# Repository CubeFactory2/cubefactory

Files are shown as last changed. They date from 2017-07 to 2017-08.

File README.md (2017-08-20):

# CubeFactory 2

The CubeFactory 2 is an autonomous and portable mini factory with own energy and material supply. It embeds three modules: a 3D-printer, a plastic recycler producing filament for the 3D-printer for closed-loop material supply as well as photovoltaic panels and batteries for energy supply. It was developed at the [Department for Assembly Technology and Factory Management of the Technische Universität Berlin](http://www.mf.tu-berlin.de/) in the frame of the [Collaborative Research Center 1026 "Sustainable Manufacturing - Shaping Global Value Creation"](http://www.sustainable-manufacturing.net).

Key figures:
* Weight:
* Dimensions: 801 x 399 x 522 mm
* Autonomy: 8 hours of printing without power supply

In this repository, you will find the complete technical documentation produced in the development of the CubeFactory 2.

## Table of contents

* [About](#about)
* [Components](#components)
* [Contribute](#contribute)
* [License](#license)
* [More information](#more-information)

## About

bild cf2

Especially in Emerging Countries there is a high demand for self-driven value creation. This is caused by an insufficient infrastructure of energy, technology and raw material. Also industrial and humanitarian supply chains are slow, difficult and expensive and equipment for value creation can be expensive and demands skills.
The motivation is that communities affected by a low standard of living or disaster are able to control their situation by manufacturing essential life-saving and life-sustaining supplies by their own.

In general, the CubeFactory 2 has the following purposes:
* Mediation of a sustain value creation
* Production of 3D printed objects by operating with disposable resources to create a sustain product
* Realization of closed loop material cycles
* Low-cost manufacturing of material and product
* Enabling small producers to access markets

## Components

The CubeFactory 2 contains all necessary infrastructure for production. It consists of the following components:
* 3D FDM printer
* Case
* Power supply, consisting of foldable solar panels and accumulator
* Recycler, consisting of PET shredder and extruder

bild cf2 detail

### Cost overview

| Component | Cost in € | Details |
|:----| ----: | :---- |
| 3D-printer | 614 | [printer readme](3d_printer) |
| Case | 250 | [case readme](case) |
| Power supply | 4430<sup>1</sup> | [power supply readme](power_supply) |
| Recycler | 1200<sup>2</sup> | [recycler BOM](recycler/BOM_WeCycler.ods) |
| **Sum** | **6494** ||

**Notes on costs:**  
1: The cost for the power supply is that high because its parts were custom made to fit into the case. Alternative solutions for the power supply such as a plug could significantly reduce the cost to a few hundred Euros.  
2: The prices for the parts of the recycler have not been completely documented yet. Therefore, the above cost for the recycler is estimated.

## Contribute

Feel free to build and futher develop the CubeFactory 2. Any improvements of the work documented here are welcome.
There is a high flexibility in terms of selecting the particular components for the CubeFactory 2. For example, the power could alternatively be sourced from a car battery or generated through wind, water or nuclear fusion. While the 3D-printer is an independent open source project, the Recycler is an own development for the use in the CubeFactory and offers a lot of room for improvement.  

## License

<br />This work is licensed under a <a rel="license" href="http://creativecommons.org/licenses/by-sa/4.0/">Creative Commons Attribution-ShareAlike 4.0 International License</a>.

## More information
* About the previous version of the CubeFactory as well as related projects such as the RecyclerBin: visit the [Cubefactory blog](http://cubefactory.org/).
* About the underlying concept: see the publication ["Realization of a Learning Environment to Promote Sustainable Value Creation in Areas with Insufficient Infrastructure"](http://www.sciencedirect.com/science/article/pii/S2212827115005399) (CC BY-NC-ND 4.0)
* About the results of the Collaborative Research Center "Sustainable Manufacturing - Shaping Global Value Creation": check the book ["Sustainable Manufacturing - Challenges, Solutions and Implementation Perspectives"](https://link.springer.com/book/10.1007/978-3-319-48514-0) (CC BY 4.0)

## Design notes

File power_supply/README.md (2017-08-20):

# Power Supply 

In order to ensure the autonomous operation of the CubeFactory 2, it has a photovoltaic generator and a battery storage system. The following remarks will give you an overview of the most important facts on the subject. 

---

### Contents

 * [Photovoltaic generator](#photovoltaic-generator)
 * [Battery storage system](#battery-storage-system)
 * [Important parameters](#important-parameters)
 * [Equipment](#equipment)
 * [Cost overview](#cost-overview)
 * [Alternative approaches](#alternative-approaches)
 
---

### Photovoltaic generator

The PV generator converts sunlight directly into electrical direct current and allows to operate the printer or charge the battery storage system. The PV generator itself consists of 3 foldable modules, which makes it possible to fit the modules, like all other components, into the case. In this way, the modules can be easily transported and, if necessary, protected against environmental influences.

---

### Battery storage system

In order to store the surplus energy generated by  PV generator, and compensate for irregularities in the power generation, the CubeFactory 2 has a lithium battery.

#### Discharge curve

The discharge curve describes the relationship between remaining capacity and operating voltage. The characteristic feature of lithium batteries is that they supply a constant voltage over the entire discharge period. The following figure shows the charging curve for a lithium battery for different C values.

N|Kurve2

The mentioned C-value indicates the factor of the battery charge quantity that is discharged per hour.

#### Calculation of the required charge quantity

The CubeFactory's battery is designed to operate the 3D printer for about *t=8* hours. In order to determine the required charge quantity *Q* the power consumption *P* and the electricity consumption *i* of the 3D printer must be known. In the case of our printer *P = 100 W* and *I = 10 A* applies. Furthermore, a battery can only be discharged to a certain degree, since otherwise the electrodes will be damaged. For lithium systems, this maximum degree of discharge *e* is at about 90%. 
With these values, the required charge quantity can be calculated and the following applies:

example

With an existing capacity of 100 Ah the requirement is fulfilled.

---

### Important parameters
The following table provides an overview of the most important parameters.

| Parameter | Value |Unit|
| :----  | :--- |:---:|
| **Photovoltaic generator** |
| Number of modules | 3 |-|
| Segments per module | 4 | - |
| Cell type | Si-mono | - |
| Rated power | 145 | W |
| Dimension unfolded | 1450 x 700 x 2.5 | mm |
| Dimension folded | 360 x 700 x 30 | mm |
| **Battery storage system** |
| Storage technology | LiFePO4 | - |
| Operating voltage | 12.8 | V |
| Charge quantity | 100 | Ah |
| Storage capacity | 1.28 | kWh |

---

### Equipment

####  Charge controller and MPPT

The MPPT charge controller fulfills several important functions, which are briefly explained below. On the one hand, it ensures that the battery (12.8V charging voltage) can be charged via the photovoltaic system (14V nominal voltage). Generally speaking, it is possible with the charge controller to charge a battery with a lower nominal voltage via a photovoltaic system with a higher nominal voltage. 

In its function as charge controller, the device ensures that charging method and charging current are selected so that the longest possible battery life is achieved. Furthermore, the control unit provides an over and deep discharge protection to prevent damage to the battery.

The last function is the function as Maximum Power Tracker (MPPT). Here, the optimum operating point is determined continuously, in which the output power is maximized.

####   MPPT control

In order to configure and evaluate the MPPT charger, an MPPT controller is used. This is a solar computer or a remote-control panel which allows to monitor the following performance parameters in real time.
*	Power of the solar module
*	Voltage of the solar module
*	Daily income in kWh
*	Display of current charging stage
*	Charging and discharging current of the battery
*	Battery voltage

In addition, it is possible to retrieve historical data from the last 30 days.

#### AC charger
In order to be able to charge the battery by alternating current via the mains, the CubeFactory 2 also has a mains charger which is designed for 100 to 240 V AC.

#### Circuit diagram

N|Kurve2

---

### Cost overview

The following table provides an overview of the cost of the energy supply system.

| Quantity | Designation | Single price in €| Total price in €|
|:----| :----  | -----: |  ---:|
| 3 | Photovoltaic generator | 780 | 2340 |
| 1 | Lithium battery | 720 | 720 |
| 1 | DC/DC converter | 80 | 80 |  
| 1 | MPPT/ charge controller | 170 | 170 |
| 1 | AC charger | 120 | 120 |
| 1 | Connection cable MPPT | 13.50 | 13.50 | 
| 1 | 8m 6mm² Solar connecting cable | 33.50 | 33.50 |
| 2 | MC4 Junction box | 8.40 | 16.80 | 
|4 | 1m 6mm² MC-4-connecting cable | 9 | 36 |
|1 | Planning and procurement | 900.20 | 900.20 | 
|| **Sum** |  |  **4430**|

The additional costs for planning and procurement are the result of the fact that the solar module is a custom-made product.

---

### Alternative approaches

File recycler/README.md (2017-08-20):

# Recycling unit
## Overview

 The recycling unit of the cubefactory 2 is able to produce filament for the 3d printer. In a two-step process plastic waste is shred into little pieces and then transformed into filament.

+ __Input:__ waste from 3d printing or other plasic e.g. from plastic bags or plastic bottles (just a single type of material)

+ __Output:__ filament that can be (spooled an then) used for FDM 3d printing 

+ Two-step __process__ realized by two independent __modules__: 
	1. Shredding the material into small pieces ([shredder](#Shredder)) 
	2. Extruding the filament ([extruder](#Extruder))

+ The [powertrain](#Power) module can be attached to either the shredder or the extruder with the purpose of saving weight and costs

+ Special requirements for the recycler to be used in the cubefactory 2:
	+ To be compact (small package)
	+ To be lightweight
	+ Low power consuption 

+ Hierarchy and foto of the realized construction (3d view [here](CAD/CAD(stl)/00_00_00-wecycler.STL)):

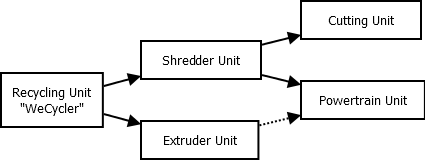
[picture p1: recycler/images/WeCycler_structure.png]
Overview Structure of Repo and Construction
 
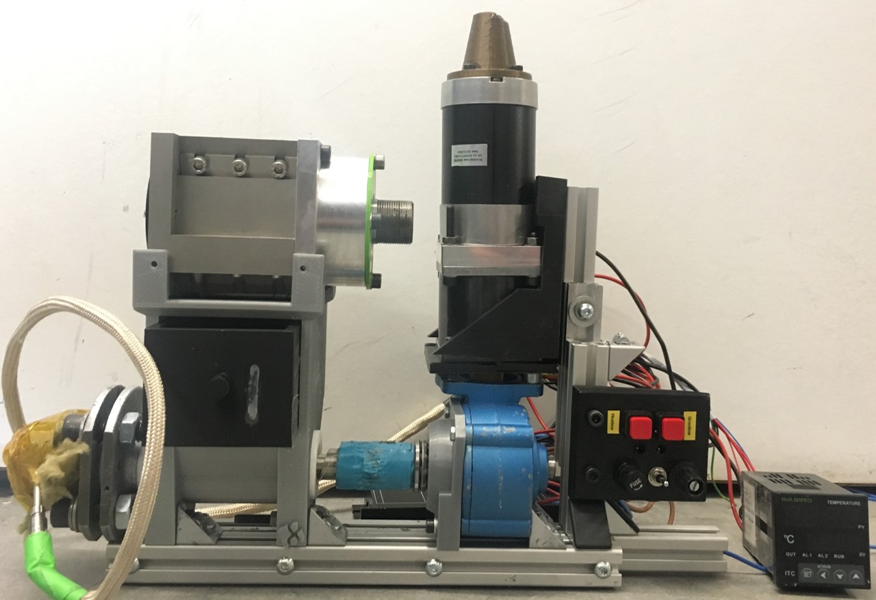
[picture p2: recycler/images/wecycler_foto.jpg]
Bild Zeichnung WeCycler


## Shredder 
### Goals and concept
The Shredder aims to mechanically shred the input material into small, similar sized pieces.

+ __Input:__ 
	+ Different plastics (as long as they are sorted, clean and dry)
	+ Possible sources could be misprints or PET bottles
+ __Output:__
	+ Smaller pieces (pellets)
	+ Pieces should hopefully be equally sized (to later get a more consistent filament)
	+ Maximum size can be limited via usage of filters
	
+ The selected __principle__ is a cutting mill with a stator and a rotor both equipped with static/ rotating blades 
+ The shredder should be __adaptable__ to process different materials and deliver variable pellet sizes
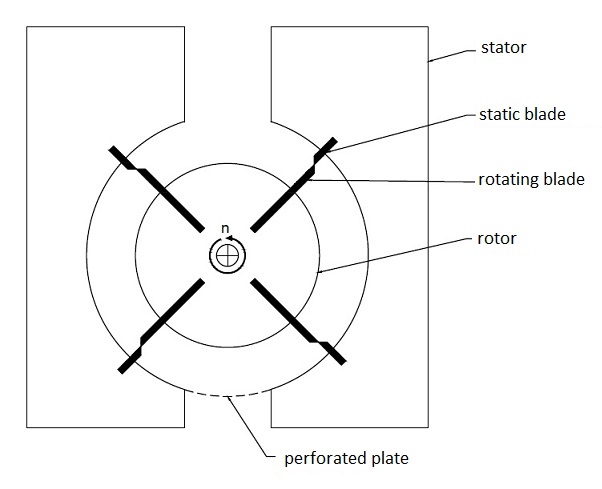
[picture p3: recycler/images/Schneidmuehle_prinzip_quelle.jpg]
Schneidmühle Prinzipskizze


### Realization
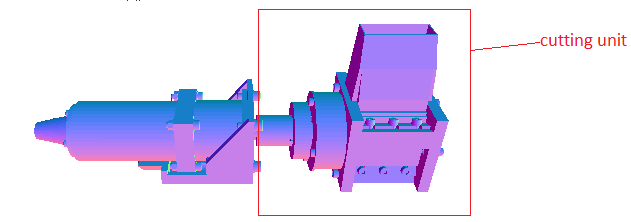
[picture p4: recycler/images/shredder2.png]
shredder

+ The rotor is realized by a used (and damaged) milling cutter  (recycling!) 
+ The other parts are special components that have been manufactured for the WeCycler
+ To adapt to different materials, the speed (rpm) of the rotor is adjustable. Furthermore static blades can be moved to to change the distance between static and dynamic blades.
+ The output pellet size is determined by selection of a changeable filter (perforated plate)
+ More detailed information about the realized shredder [here](Shredder_Info.md)
 
## Extruder 
### Goals and concept
The extruder produces filament from pellets using pressure and heat.

+ __Input:__ pellets or shredded material (equally small sized and just one type of material)
+ __Output:__ filament
+  The extruder __process:__ [(explanation video)](https://www.youtube.com/watch?v=WaB-dsB1Kfk)

	1. Feeding the material into a hopper
	2. The pellets are moved through a tube by a spinning screw
	3. The plasic melts due to the use heating elements along the tube an the pressure resulting from decreasing distance between screw and tube
	4. Finally the meltet material is pressed trough a nozzle, forming a string of filament
	 
+ The extruder should be __adaptable__ to process different materials and pellet sizes. Also the diameter of the filament should be variable.

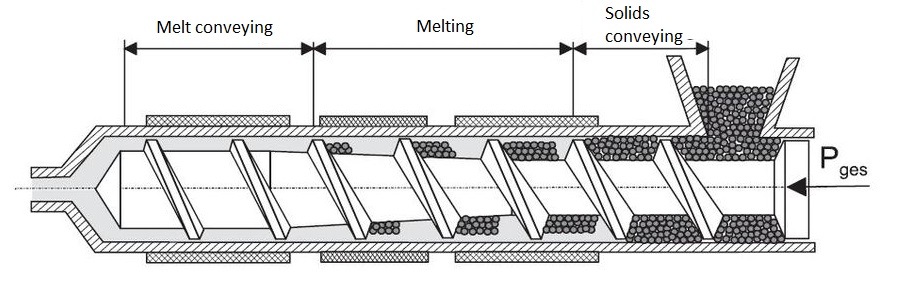
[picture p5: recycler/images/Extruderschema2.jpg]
Extruder Prinzipskizze
(__TODO__ Bildquelle))

### Realization 
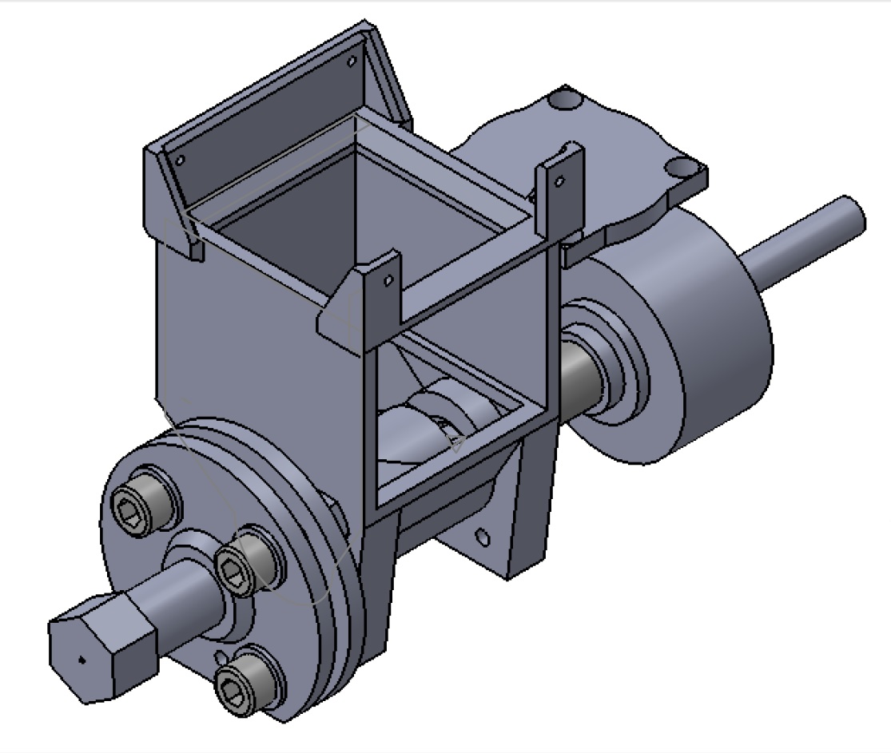
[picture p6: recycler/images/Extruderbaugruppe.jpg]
Extrudergruppe
(__TODO__ Bildquelle, Beschriftung der Einzelteile?))

+ More detailed information on the single parts of the realized extruder unit [here](Extruder_Info.md)
 
## Powertrain 
+ For more information on the powertrain unit see [here](Powertrain_Info.md).
+ The powertrain can be attached in 2 different positions: either it drives the the shredder (pink) or the extruder (green). This is due to the need of saving money, space and weight.

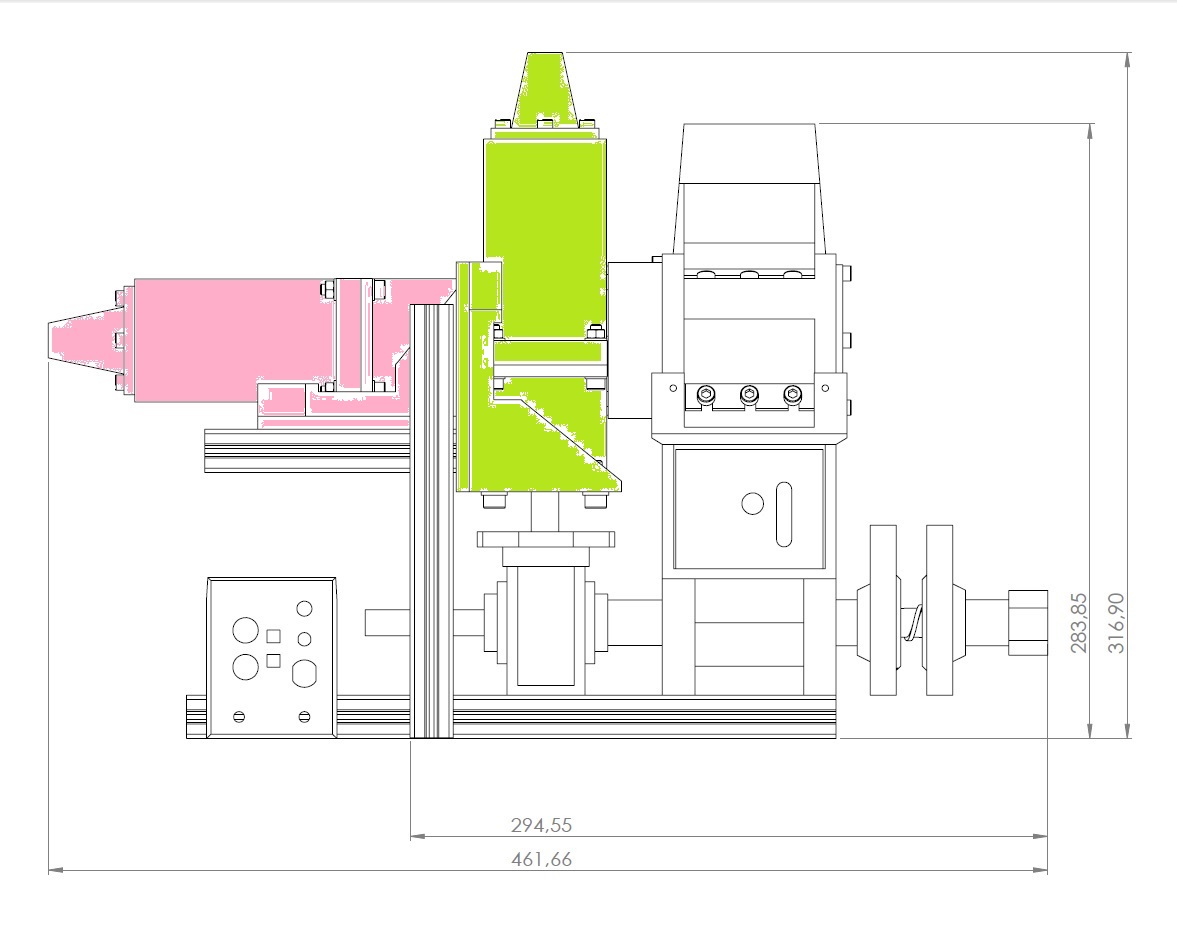
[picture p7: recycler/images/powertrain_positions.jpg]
positions

### This Repository
+  Exploded views [here](CAD/exploded_views)
+  Bill of Materials [here](BOM_WeCycler.ods)
+  CAD files [here](CAD)

### More Information
+ https://www.3dhubs.com/talk/thread/which-shredding-and-extruding-machines-are-available-part-3
+ https://www.3dhubs.com/talk/thread/how-does-local-recycling-work-part-2

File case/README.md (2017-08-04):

# Case

Case|1

In order to protect the components of the CubeFactory 2 during transportation and  from extreme environmental influences, the components are placed in a case. The case therefore represents the system boundary of the CubeFactory 2. 
A mandatory requirement of the CubeFactory 2 is the possibility of transportation by one person. The fulfillment  of this requirement had to be realized by selecting a suitable case. For this purpose, the chosen model has rollers and a pull-out handle.

### Important parameters

The following table provides an overview of the most important parameters.

| Parameter | Value |Unit|
| :----  | :--- |:---:|
| Inner dimensions | 737 x 356 x 457 | mm |
| Outer dimensions | 801 x 399 x 522 | mm |
| Weight | 11.3 | kg |
| Protection class | IP67 |-|
| Price | 250 | EUR |

#### Degree of protection 

In the original state, the case has protection class IP67. By screwing the components in the case, this protection is lost, but the case is still protected to IP65.
The degree of protection describes the suitability of a device for various environmental conditions, more precisely the protection against direct contact or penetration of solids and liquids. For our case only the last two are relevant.
The degree of protection 65 covers the protection against dust (dustproof) and the protection against water jets.

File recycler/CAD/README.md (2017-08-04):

## How To

__For an online overview:__ browse the CAD(stl)-folder, where you can see 3d-views of every part and the corresponding exploded views

__Or download:__ 

+ the CAD(step) folder (same structure as STL folder but without exploded views)

+ the CAD(solidworks) folder (particular structure, no information loss)  

__Open/Manipulate the files:__ We used the open-source 3D modeler _[FreeCAD](https://www.freecadweb.org/)_ to work with the STEP- and STL-files. If you have access to the commercial Software _[SolidWorks](https://en.wikipedia.org/wiki/SolidWorks)_, you should use the corresponding files to avoid information loss.

__Nomenclature__ of the CAD parts: XX_YY_ZZ-name_of_part_or_assembly.STL, where
+ XX is the number of the main assembly
+ YY is the number of the subassembly
+ ZZ is the number of the part

The nomenclature also appears in the [BOM]().  
__TODO__ Add link to BOM

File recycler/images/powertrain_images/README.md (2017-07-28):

put here images (and equations) for the drivetrain readme

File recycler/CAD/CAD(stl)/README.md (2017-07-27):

[3D View Assembly (STL)](00_00_00-wecycler.STL)

[3D View Explosion (STL)](00_00_00-wecycler(explosion).STL)

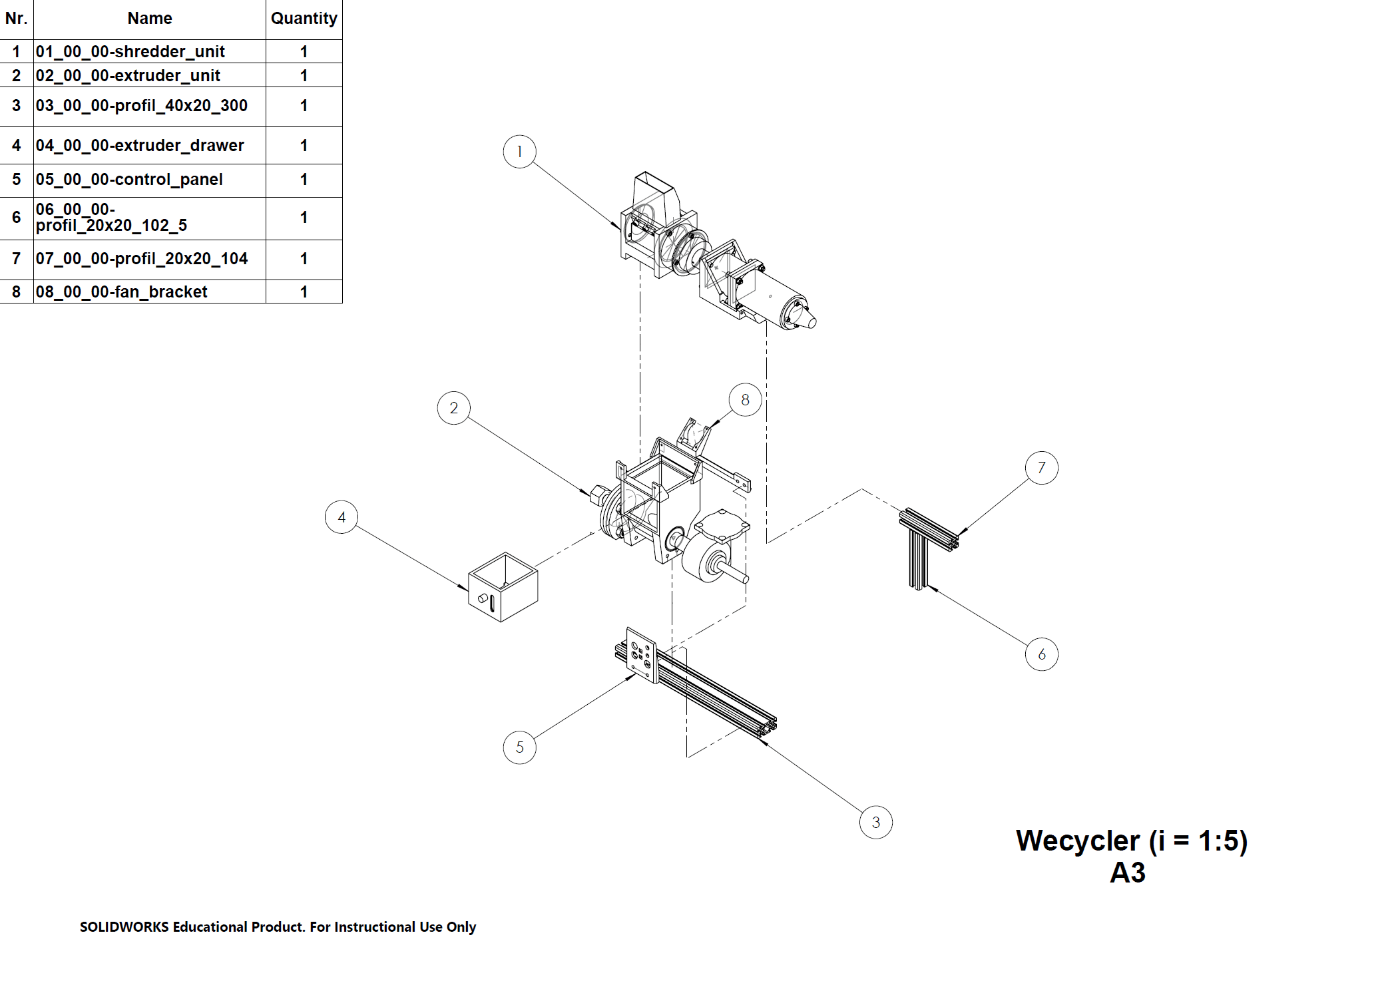
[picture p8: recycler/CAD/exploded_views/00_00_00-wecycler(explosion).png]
here


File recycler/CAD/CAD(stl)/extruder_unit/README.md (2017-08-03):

[3D View Assembly (STL)](02_00_00-extruder_unit.STL)

[3D View Explosion (STL)](02_00_00-extruder_unit(explosion).STL)

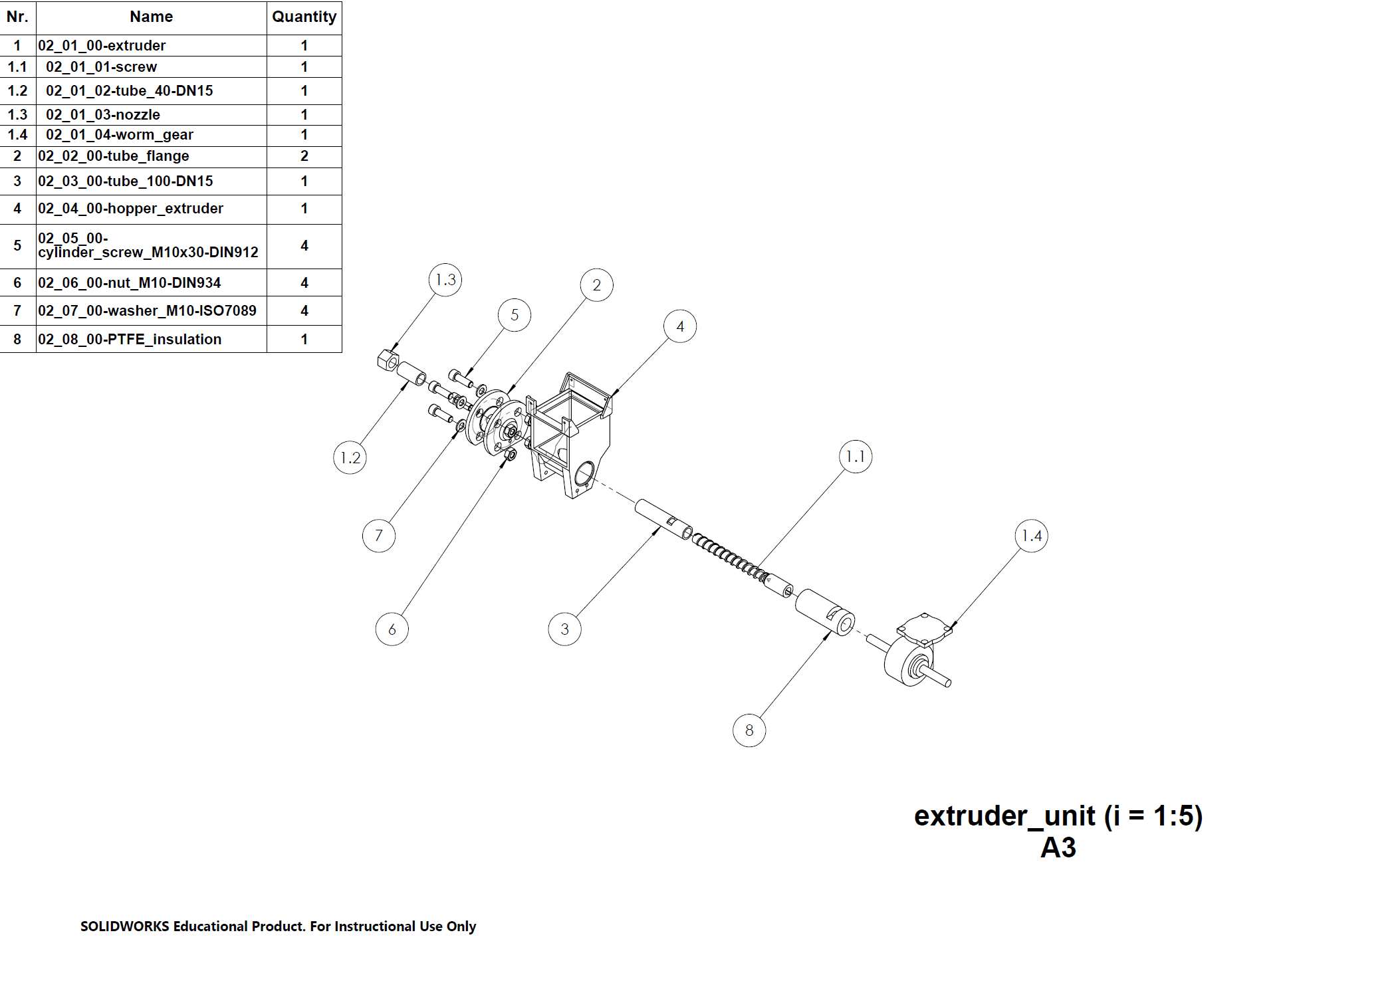
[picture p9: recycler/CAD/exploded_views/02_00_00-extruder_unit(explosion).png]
here


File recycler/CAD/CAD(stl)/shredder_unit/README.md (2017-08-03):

[3D View Assembly (STL)](01_00_00-shredder_unit.STL)

[3D View Explosion (STL)](01_00_00-shredder_unit(explosion).STL)

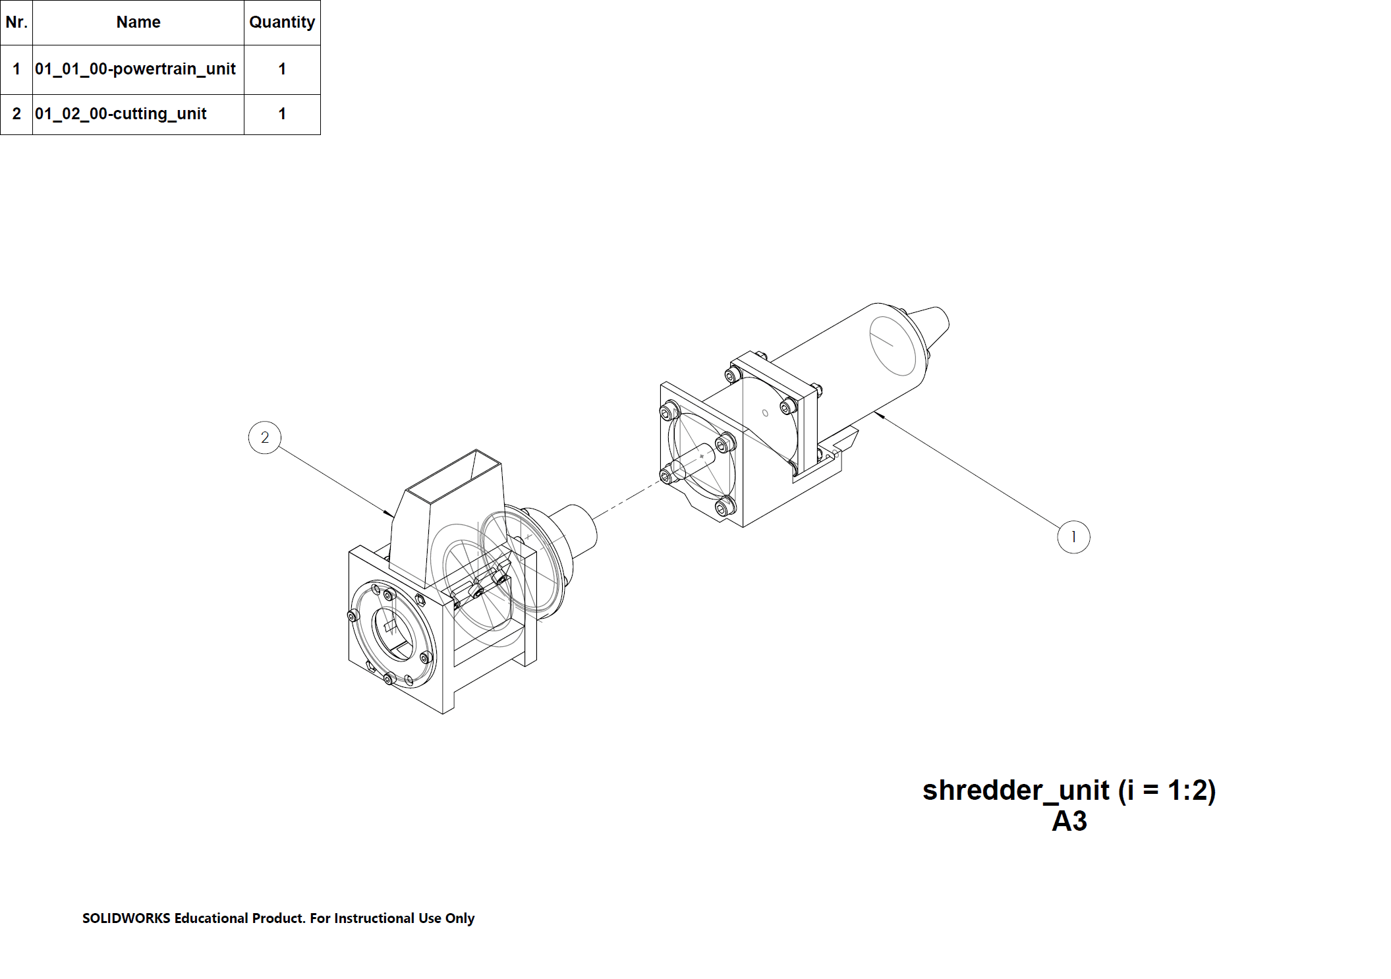
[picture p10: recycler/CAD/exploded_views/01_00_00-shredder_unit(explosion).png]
here


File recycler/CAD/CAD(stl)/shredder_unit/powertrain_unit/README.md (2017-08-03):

[3D View Assembly (STL)](01_01_00-powertrain_unit.STL)

[3D View Explosion (STL)](01_01_00-powertrain_unit(explosion).STL)

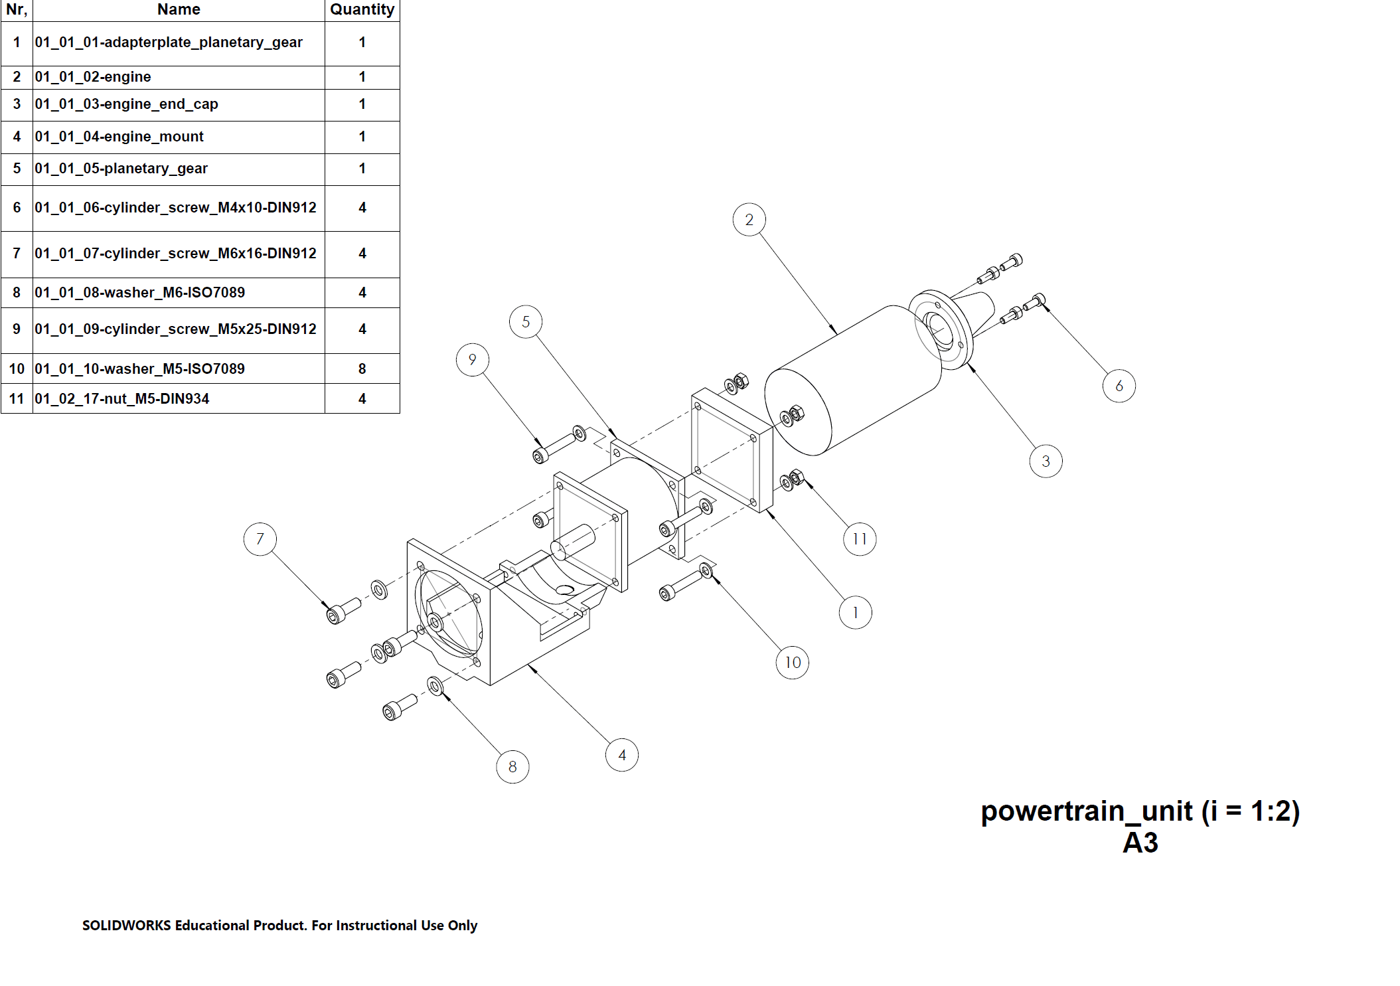
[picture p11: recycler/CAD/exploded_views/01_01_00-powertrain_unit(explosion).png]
here


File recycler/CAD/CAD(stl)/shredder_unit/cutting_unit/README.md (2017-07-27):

[3D View Assembly (STL)](01_02_00-cutting_unit.STL)

[3D View Explosion (STL)](01_02_00-cutting_unit(explosion).STL)

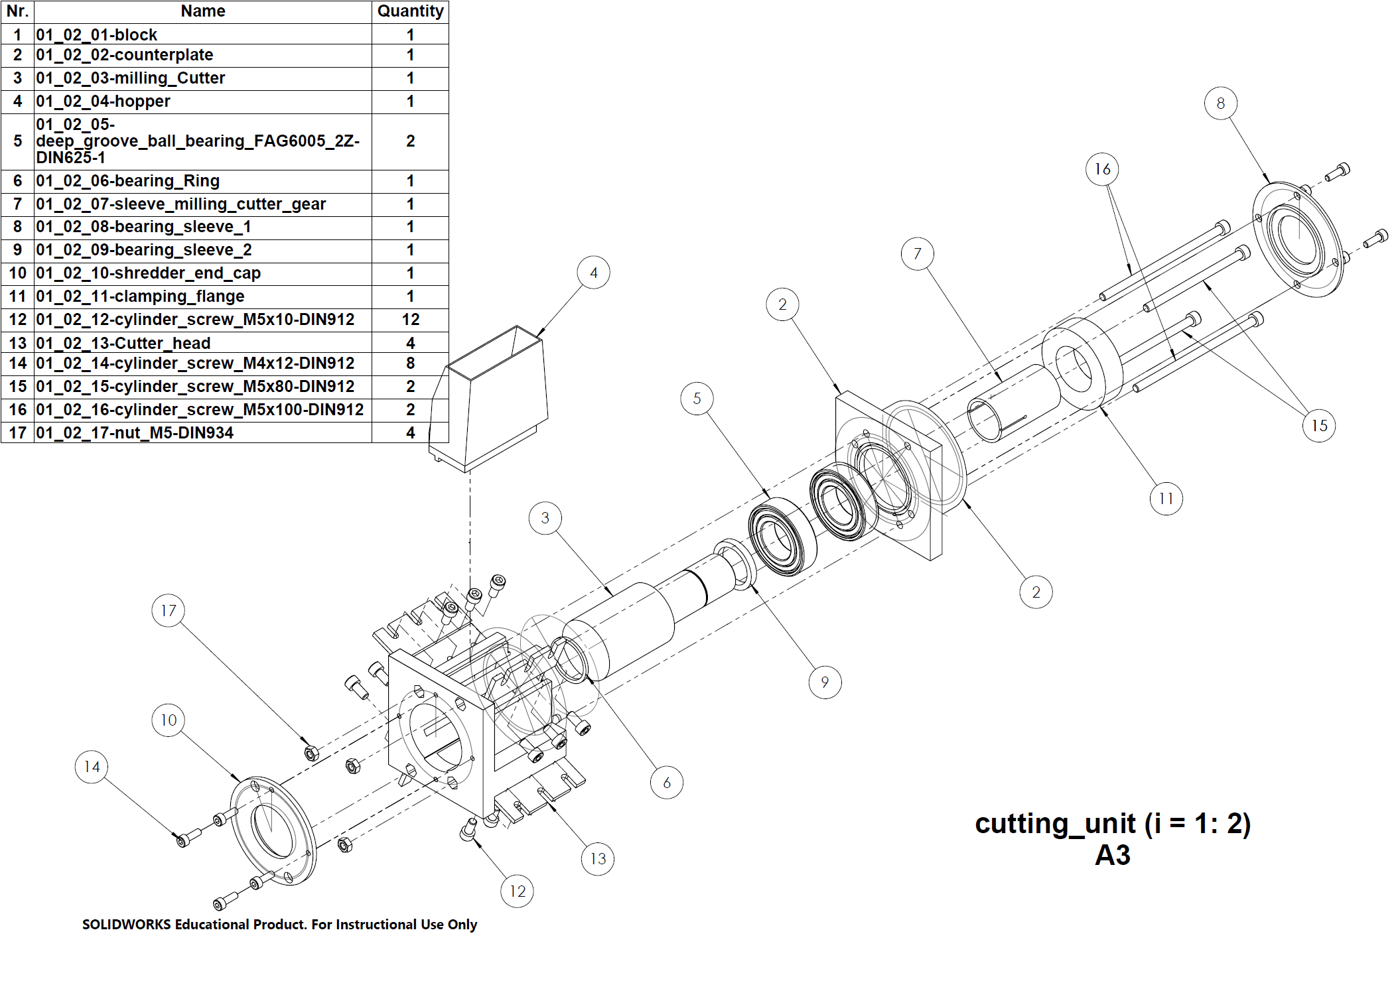
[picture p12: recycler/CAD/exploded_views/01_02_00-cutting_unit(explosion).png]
here


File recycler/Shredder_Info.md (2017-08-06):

## More information about the parts of the shredder unit
+ Drawing of the shredder unit: [here](drawings/01_00_00-shredder_unit.PDF)

+ The damaged end face __milling cutter__ that is used as rotor/ dynamic blades:
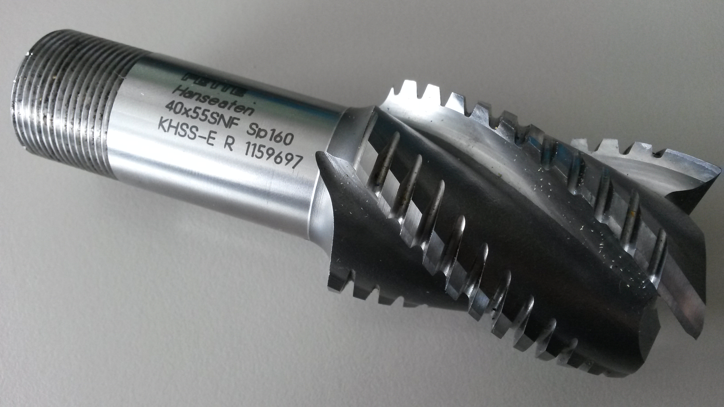
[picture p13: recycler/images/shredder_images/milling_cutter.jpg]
milling cutter
 
	+ Type : Fette Hanseaten 40x55SNF Sp160

	* The spiral form of the blades allows a nearly continous cutting process and helps to prevent shock loads. 

+ The the __block__ for the housing (custom product) that holds the static blades
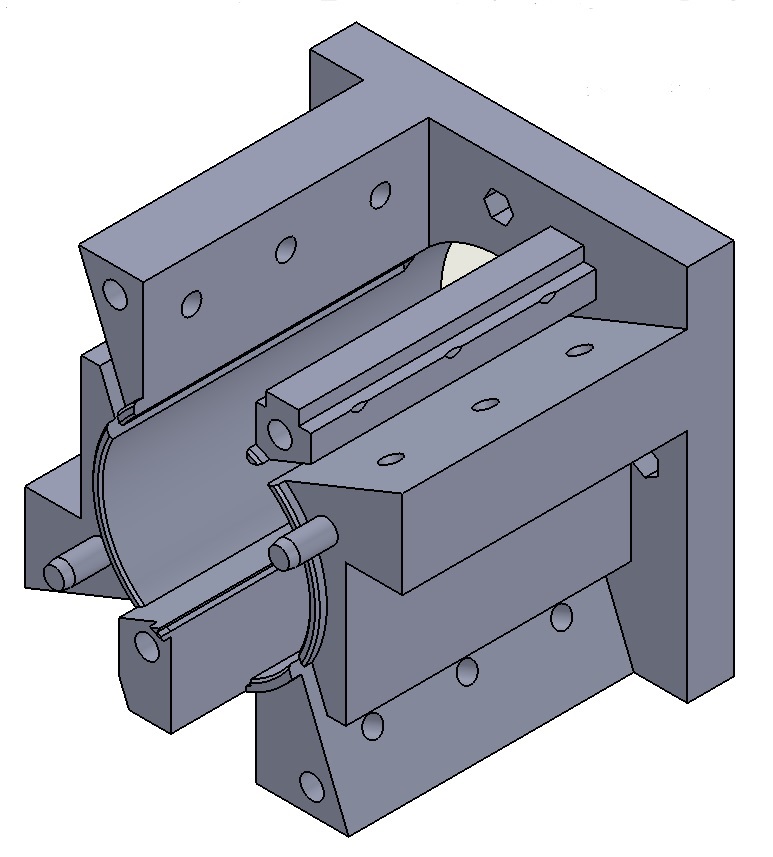
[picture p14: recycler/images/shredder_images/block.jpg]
block
 
	+ Drawing: [here](drawings/01_02_01-block.PDF)
	
	* Material: 1.4404 - X 2 CrNiMo 17 13 2
	
	* The block was printed (selective laser sintering). The previous model was a welded construction but this method caused too many tensions. We also thought about milling and turning but the process would be too complicated (many changes of the fixing).
	
	* The four static blades are attached to the block by three screws each. This fixing method allows us to adapt the blade position to wear or and to compensate tolarances. In addition an adption to different pellet materials is possible.

+ The __counterplate__ (custom product) that holds the bearings
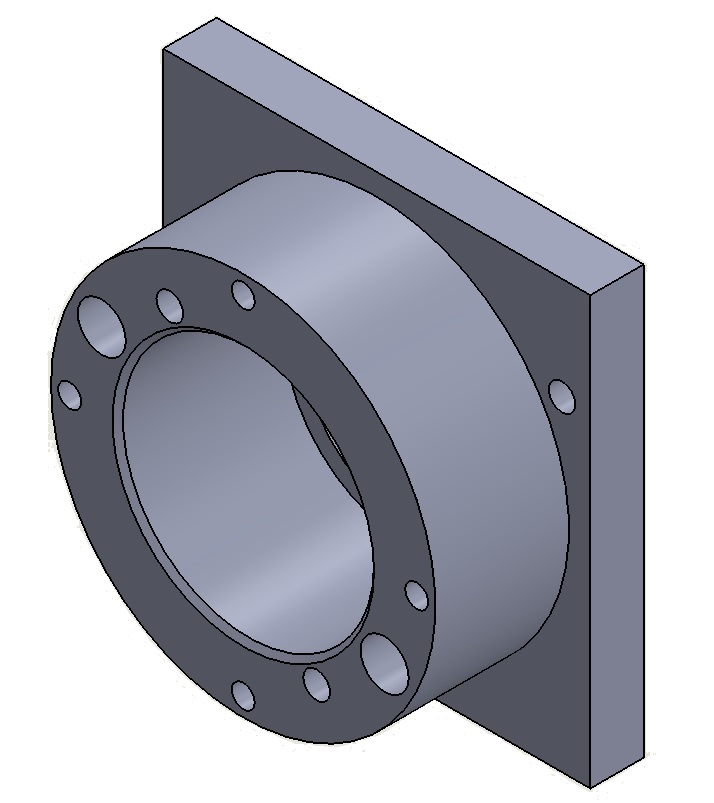
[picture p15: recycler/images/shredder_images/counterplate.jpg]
counterplate

	+ Drawings: [here](drawings/01_02_02-counterplate.PDF) and [here](drawings/01_02_02-counterplate_DETAILS.PDF)
	+ Material: aluminium
	+ Production method: milling
	+ Bearing: FAG 6005 (radial deep groove ball bearing)
	+ We used a floating bearing arrangement because its cheap and there is no need for low tolearances in the axial movement of the milling cutter.

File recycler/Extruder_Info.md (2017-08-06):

## More information about the parts of the extruder unit

+ The used extruder screw (custom part) with three zones:
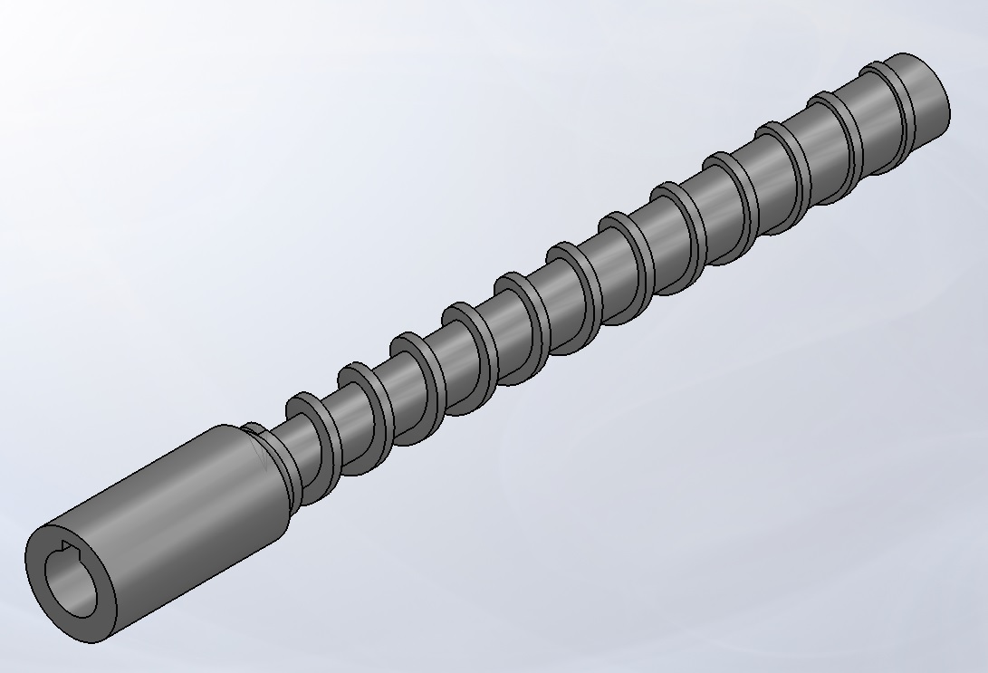
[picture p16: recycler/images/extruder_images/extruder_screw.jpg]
screw


+ The heating sleeve and the nozzle:
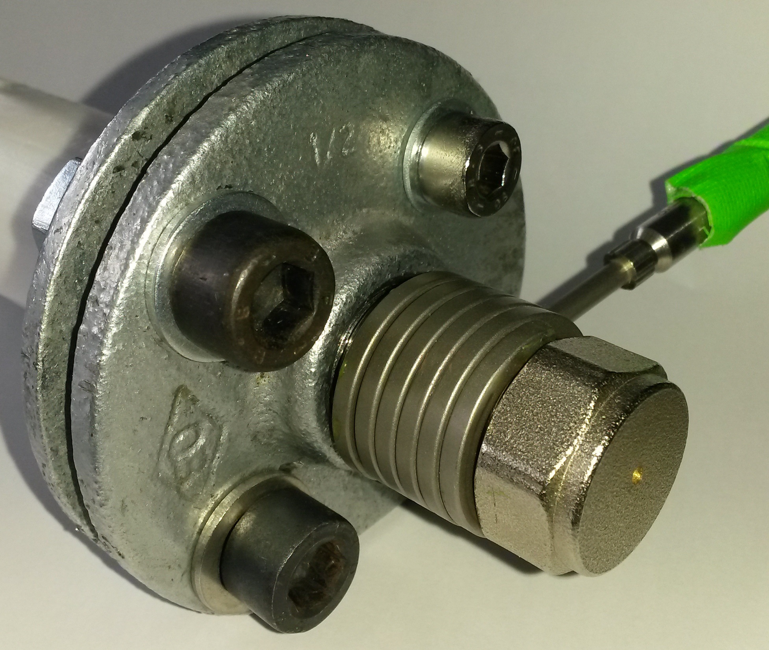
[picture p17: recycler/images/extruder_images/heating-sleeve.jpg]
heating-sleeve


+ The thermal barrier to prevent the heating sleeve from from heating the hopper and melting the pellets before reaching the screw:
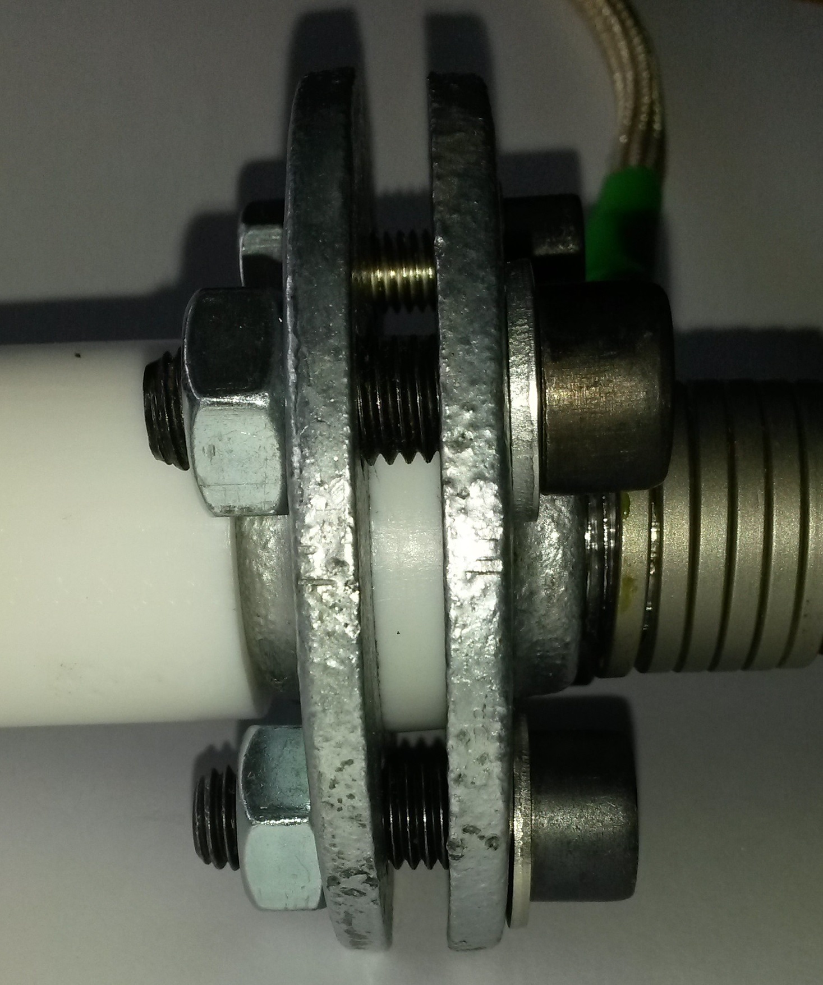
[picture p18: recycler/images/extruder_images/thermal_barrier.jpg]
barrier


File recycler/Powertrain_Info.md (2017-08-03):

# Motor, heater and electronics
## Motor
  The Cubefactory 2 uses a dc motor called „RS Pro brushless dc motor". The new engine was selected based on calculations and general demands regarding mass and installation space.
  
???Thereby a minimum requirement of 0,88 Nm was determined fort he forque to punch and cut ABS and PLA plastics.
2.544 N/Min with rotary energy of 167W/2Nm without gearing mechanism
0,08 Nm with gearing mechanism???

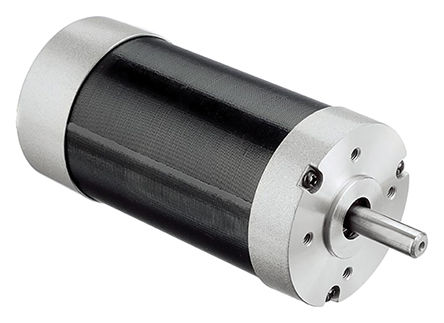
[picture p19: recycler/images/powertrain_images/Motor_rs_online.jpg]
Powertrain image


Characteristic values:
+ voltage: 24 volt (dc)
+ current (norm.): 10 ampere
+ current (max.): 40 ampere
+ electrical power (norm.): 240 watt
+ torque (norm.): 0,44 newton metre
+ torque (max.): 1,76 newton metre
+ maximum speed: 3500 1/minute

## Planetary gear
  For the gear reduction of the powertrain a planetary gear (i=10:1) is used to lower the speed and reduce the shear strength of the synthetic material simultaneously. An experiment proofed that the shear strength of the two synthetic materials ABS and PLA sinks at a lower speed and therefore less cutting force for the shredding process of the synthetic material is required.

## Motor controller
  Brushless DC motors such as being built in this Recycler work on the functional principle of a three-phase synchronous motor. The engine is set in motion by excitation from permanent magnets. Besides, voltage is used to generate a rotary magnetic field in the stator and to drive the engine. Therefore the engine can be steered via voltage coming from a motor controller. This kind of controller switches the voltage to the single windings and varies the speed of the engine, in the simplest case depending on the DC voltage at the input.
 
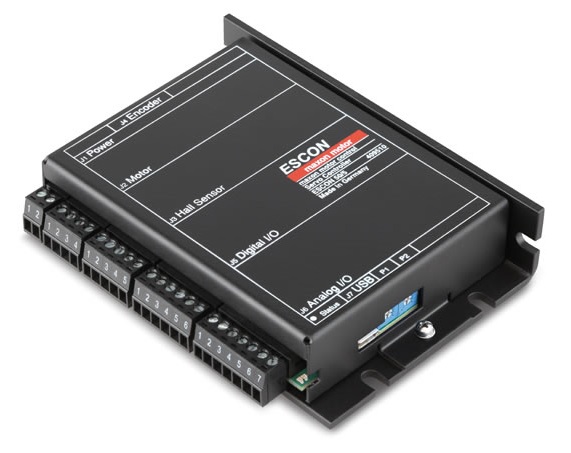
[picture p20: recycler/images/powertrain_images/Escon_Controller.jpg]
Motor Controller image

 
Maxon Motor AG´s  ESCON 70/10 is used as engine controller. This controller enables the user to vary the motor speed by an analogous potentiometer or an external control voltage at a constant external direct voltage. It is also possible to fix minimal and maximum speed of the engine with a software and to stop the engine immediately. By using this function a safety key can be implemented with emergency stop.

## The heating sleeve

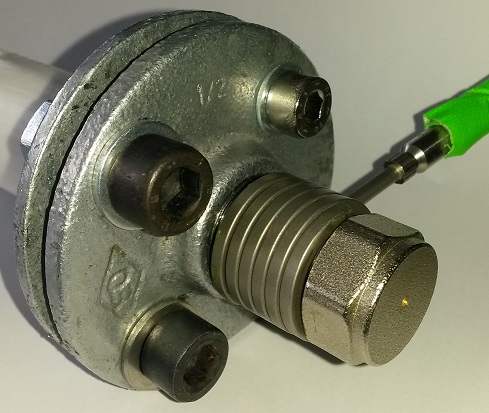
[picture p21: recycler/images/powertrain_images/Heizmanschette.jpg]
heating sleeve


  The extrusion is heated up by an electric heating sleeve. It can be operated like the powertrain with 24 volts of DC voltage to avoid electric conversion losses and has a maximum power consumption of 150 watt. It can generate temperatures up to about 250°C. The inner diameter measures 21 mm and corresponds to the external diameter of the extruder tube. The heating cuff features a temperature sensor which ensures better temperature controlling.
  
## Temperature control

  The temperature setting and its supervision is carried out by a temperature controller from the company Inkbird called „D1S-2R-24“ which has an operating voltage of 24 volts DC. The target temperature can be adjusted and the actual temperature can be supervised by the display.

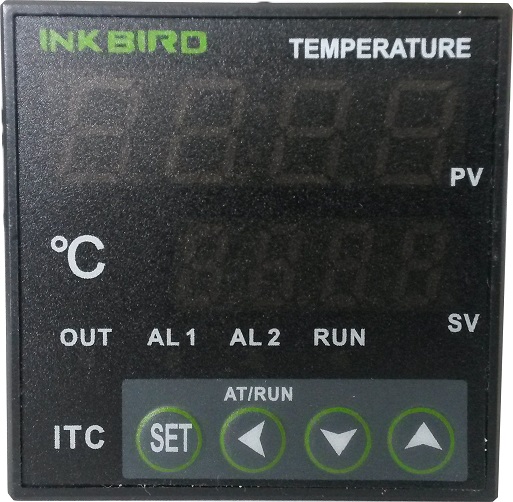
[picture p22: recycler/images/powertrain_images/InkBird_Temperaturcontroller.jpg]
temperature control


## Electric circuit
  For a better understanding oft the electric circuit two views can be used.
Whereas the first view shows the circuit oft the electronics, the second diagram supports the visual components for the motor controller. 

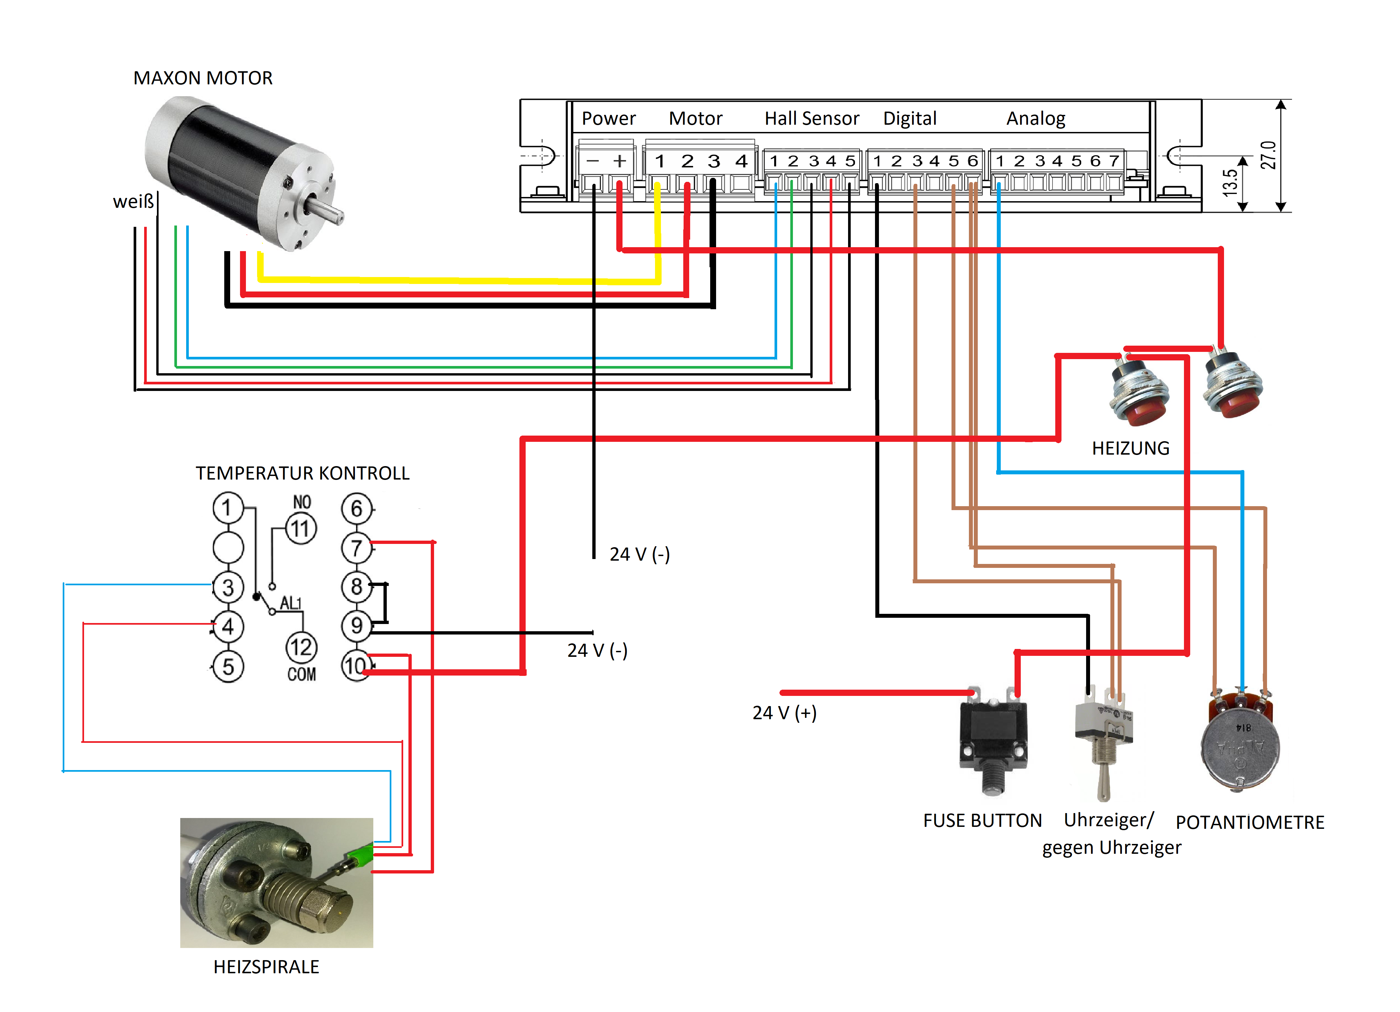
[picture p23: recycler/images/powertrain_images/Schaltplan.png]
Electric circuit 1


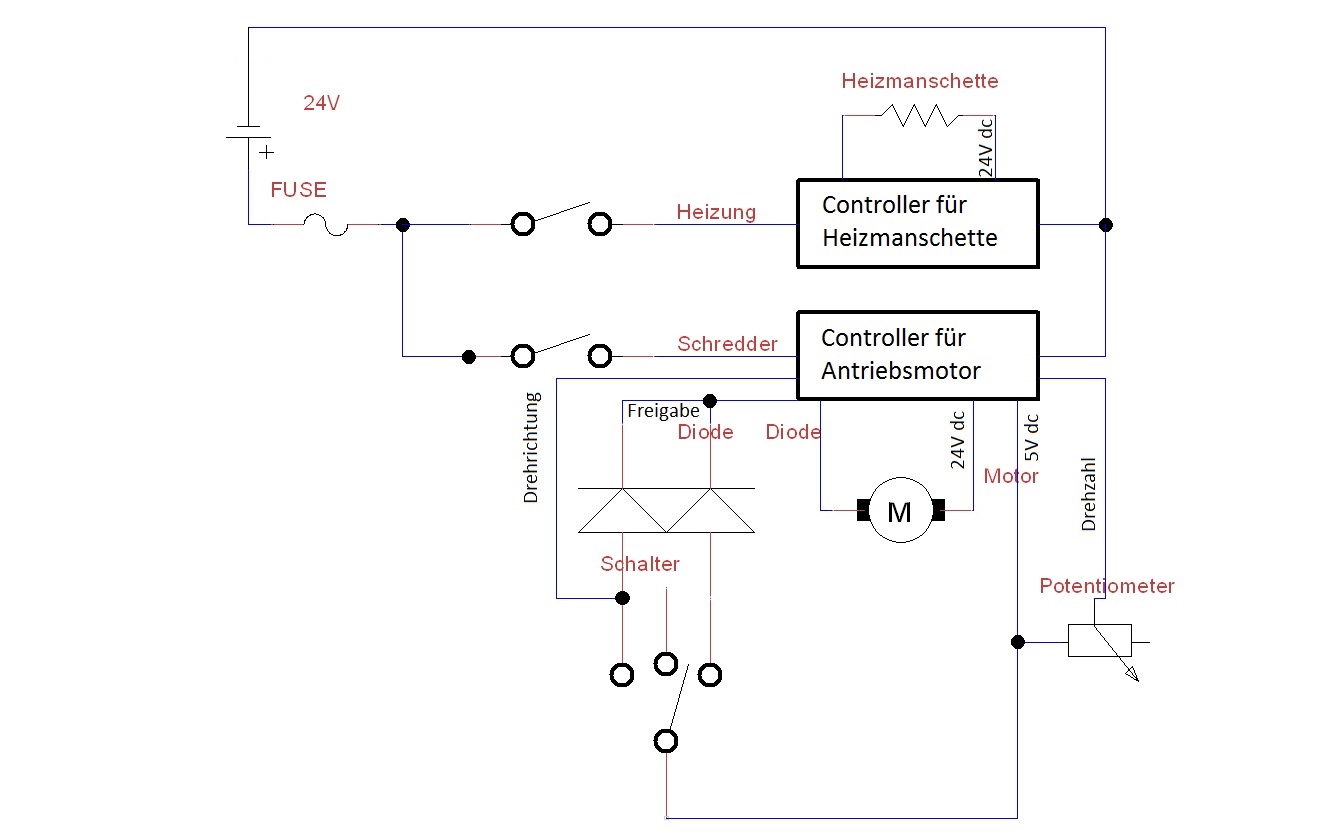
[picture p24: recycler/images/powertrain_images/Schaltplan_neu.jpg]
Electric circuit 2


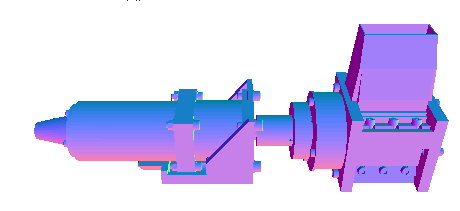
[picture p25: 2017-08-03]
recycler/images/shredder.png

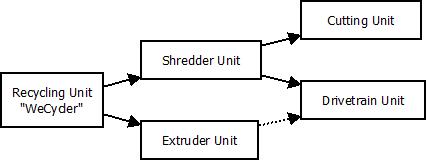
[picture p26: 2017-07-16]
recycler/images/WeCycler_structure.jpg

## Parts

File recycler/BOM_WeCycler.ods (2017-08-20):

Item number |  |  | Name of part | Norm/material/size | Note | Quantity | Cost | CAD-Name
0 |  |  | wecycler |  |  | 1 |  | 00_00_00-wecycler
1 |  |  | shredder unit |  |  | 1 |  | 01_00_00-shredderunit
 | 1.1 |  | powertrain unit |  |  | 1 |  | 01_01_00-drivetrainunit
 |  | 1.1.1 | adapterplate for the planetary gear | aluminium |  | 1 | ??? | 01_01_01-adapterplate_planetary_gear
 |  | 1.1.2 | engine | "RS Pro Gleichstrommotor bürstenlos", 24 Volt, 240 Watt, 3500 1/Minute |  | 1 | ??? | 01_01_02-engine
 |  | 1.1.3 | engine end cap | PLA / PMMA |  | 1 | ??? | 01_01_03-engine_end_cap
 |  | 1.1.4 | engine mount |  |  | 1 | ??? | 01_01_04-engine_mount
 |  | 1.1.5 | planetary gear |  | i=10:1 | 1 | ??? | 01_01_05-planetary_gear
 |  | 1.1.6 | cylinder screw | DIN 912, M4x10 |  | 4 | 0,04 € | 01_01_06-cylinder_screw_M4x10-DIN912
 |  | 1.1.7 | cylinder screw | DIN 912, M6x16 |  | 4 | 0,07 € | 01_01_07-cylinder_screw_M6x16-DIN912
 |  | 1.1.8 | washer | ISO 7089, 140 HV, M6 |  | 4 | 0,01 € | 01_01_08-washer_M6-ISO7089
 |  | 1.1.9 | cylinder screw | DIN 912, M5x25 |  | 4 | 0,05 € | 01_01_09-cylinder_screw_M5x25-DIN912
 |  | 1.1.10 | washer M5 | ISO 7089, 140 HV |  | 8 | 0,01 € | 01_01_10-washer_M5-ISO7089
 |  | 1.1.11 | nut M5 | DIN 934 |  | 4 | 0,05 € | 01_01_10-nut_M5-DIN934
 |  | 1.1.12 | toggle switch |  | on/off switch | 2 | 0,50 €
 |  | 1.1.13 | reversing switch |  | direction of rotation | 1 | ???
 |  | 1.1.14 | potentiometer |  | speed controller | 1 | ???
 |  | 1.1.15 | LED |  | operating display | 2 | 0,01 €
 |  | 1.1.16 | fuse-housing |  | including. fuse 10A | 1 | ???
 |  | 1.1.17 | power cable | copper |  | 1 | 2,00 €
 |  | 1.1.18 | diode |  |  | 2 | 0,15 €
 |  | 1.1.19 | fan |  | for cooling of the filaments | 1 | ???
 |  | 1.1.20 | motor controller | ESCON 70/10 |  | 1 | 496,00 €
 | 1.2 |  | cutting unit |  |  | 1 |  | 01_02_00-cutting_unit
 |  | 1.2.1 | block |  | production by IPK | 1 | ??? | 01_02_01-block
 |  | 1.2.2 | counterplate |  | production by IPK | 1 | ??? | 01_02_02-counterplate
 |  | 1.2.3 | milling Cutter |  | Fette Hanseaten 40x55SNF Sp160 | 1 | ??? | 01_02_03-milling_Cutter
 |  | 1.2.4 | hopper | PLA |  | 1 | ??? | 01_02_04-hopper
 |  | 1.2.5 | deep groove ball bearing | DIN 625-1, FAG 6005-2Z |  | 2 | 4,51 € | 01_02_05-deep_groove_ball_bearing_FAG6005_2Z-DIN625-1
 |  | 1.2.6 | bearing ring | PLA |  | 1 | ??? | 01_02_06-bearing_Ring
 |  | 1.2.7 | sleeve for the milling cutter gear |  |  | 1 | ??? | 01_02_07-sleeve_milling_cutter_gear
 |  | 1.2.8 | bearing sleeve 1 |  |  | 1 | ??? | 01_02_08-bearing_sleeve_1
 |  | 1.2.9 | bearing sleeve 2 |  |  | 1 | ??? | 01_02_09-bearing_sleeve_2
 |  | 1.2.10 | shredder end cap | PLA / PMMA |  | 1 | ??? | 01_02_10-shredder_end_cap
 |  | 1.2.11 | clamping flange |  |  | 1 | ??? | 01_02_11-clamping_flange
 |  | 1.2.12 | cylinder screw | Din 912, M5x10 |  | 12 | 0,05 € | 01_02_12-cylinder_screw_M5x10-DIN912
 |  | 1.2.13 | cutter head | steel |  | 4 | ??? | 01_02_13-Cutter_head
 |  | 1.2.14 | cylinder screw | Din 912, M4x12 |  | 8 | 0,03 € | 01_02_14-cylinder_screw_M4x12-DIN912
 |  | 1.2.15 | cylinder screw | Din 912,M5x80 |  | 2 | 0,19 € | 01_02_15-cylinder_screw_M5x80-DIN912
 |  | 1.2.16 | cylinder screw | Din 912, M5x100 |  | 2 | 0,32 € | 01_02_16-cylinder_screw_M5x100-DIN912
 |  | 1.2.17 | nut M5 | DIN 934 |  | 4 | 0,05 € | 01_02_17-cylinder_screw_M5x100-DIN912
 |  | 1.2.18 | clamping ring | steel C45 | including two screws | 1 | 7,00 €
 |  | 1.2.19 | perforated plate | 1mm steel | diameter 2mm | 1 | ???
2 |  |  | extruder unit |  |  | 1 |  | 02_00_00-extruder unit
 | 2.1 |  | extruder | DN15 |  | 1 |  | 02_01_00-extruder
 |  | 2.1.1 | screw | Edelstahl 1.4305 |  | 1 | ??? | 02_01_01-screw
 |  | 2.1.2 | tube | EN 10255-M / galvanised steel, 40mm |  | 1 | ??? | 02_01_02-tube_40-DN15
 |  | 2.1.3 | nozzle |  |  | 1 | ??? | 02_01_03-nozzle
 |  | 2.1.4 | worm gear |  |  | 1 | ??? | 02_01_04-worm_gear
 | 2.2 |  | tube flange | EN 10242 / galvanised steel |  | 2 | ??? | 02_02_00-tube_flange
 | 2.3 |  | tube | EN 10255-M / galvanised steel, 100mm |  | 1 | ??? | 02_03_00-tube_100-DN15
 | 2.4 |  | hopper (extruder) | PLA |  | 1 | ??? | 02_04_00-hopper_extruder
 | 2.5 |  | cylinder screw | Din 912, M10x30 |  | 4 | 0,19 € | 02_05_00-cylinder_screw_M10x30-DIN912
 | 2.6 |  | nut | DIN 934, M10 |  | 4 | 0,04 € | 02_06_00-nut_m10-DIN934
 | 2.7 |  | washer | ISO 7089, 140 HV, M10 |  | 4 | 0,01 € | 02_07_00-washer_M10-ISO7089
 | 2.8 |  | PTFE insulation | PTFE |  | 1 | ??? | 02_08_00-PTFE_insulation
 | 2.9 |  | thermal barrier | PTFE | between 2.3 and 2.1.2 | 1 | ???
 | 2.10 |  | heating sleeve |  |  | 1 | ???
 | 2.11 |  | temperature control | D1S-2R-24 |  | 1 | 28,00 €
 | 2.12 |  | feather key | steel | for 2.1.4 | 1 | ???
3 |  |  | Item_40x20_300 |  |  | 1 | ??? | 03_00_00-profil_40x20_300
4 |  |  | extruder drawer | PLA / PMMA |  | 1 | ??? | 04_00_00-extruder_drawer
5 |  |  | control panel | PLA |  | 1 | ??? | 05_00_00-control_panel
6 |  |  | profil_20x20_102_5 | aluminium |  | 1 | ??? | 06_00_00-profil_20x20_102_5
7 |  |  | profil_20x20_104 | aluminium |  | 1 | ??? | 07_00_00-profil_20x20_104
8 |  |  | fan bracket | PLA |  | 1 | ??? | 08_00_00-fan_bracket
9 |  |  | angle Bracket Set | M5 | 3x for the hopper, 4x for the engine mount | 7 | ???
10 |  |  | slot Nut | M5 |  | 4 | ???
11 |  |  | clamping angle M5 | M5 | at the clamping ring | 3 | ???
12 |  |  | cylinder screw | M5x15 |  | 2 | ???

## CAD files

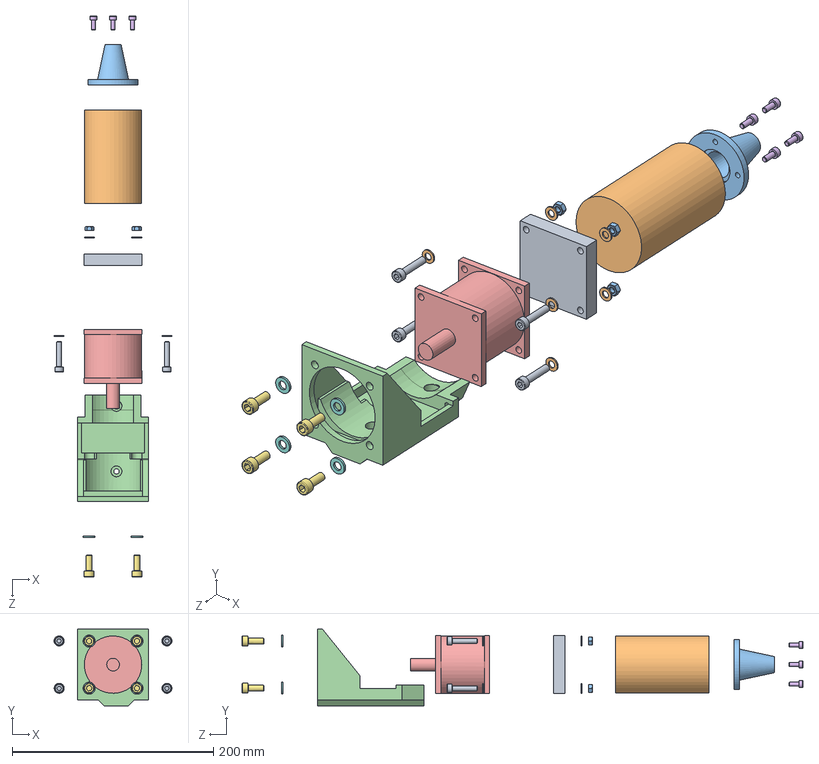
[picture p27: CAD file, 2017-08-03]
recycler/CAD/CAD(solidworks)/powertrain_unit/01_01_00-powertrain_unit.SLDASM
117.1 x 76.3 x 557.2 mm
01_01_01-adapterplate_planetary_gear
01_01_02-engine
01_01_03-engine_end_cap
01_01_04-engine_mount
01_01_05-planetary_gear
01_01_06-cylinder_screw_M4x10-DIN912 x 4
01_01_07-cylinder_screw_M6x16-DIN912 x 4
01_01_08-washer_M6-ISO7089 x 4
01_01_09-cylinder_screw_M5x25-DIN912 x 4
01_01_10-washer_M5-ISO7089 x 8
01_02_17-nut_M5-DIN934 x 4

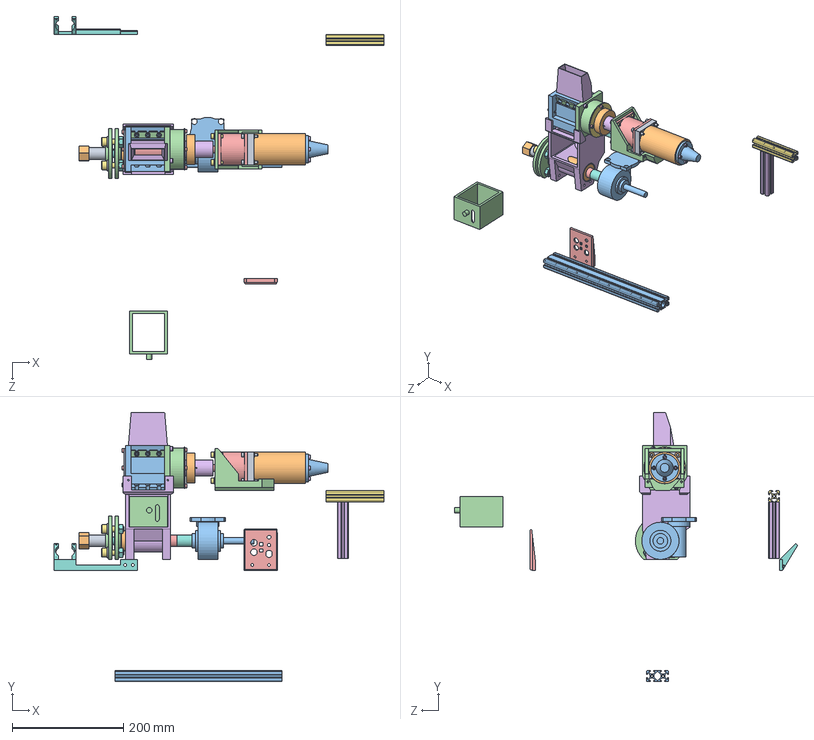
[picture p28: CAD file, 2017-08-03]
recycler/CAD/CAD(solidworks)/WeCycler/00_00_00-wecycler.SLDASM
594.0 x 484.7 x 618.0 mm
01_01_01-adapterplate_planetary_gear
01_01_02-engine
01_01_03-engine_end_cap
01_01_04-engine_mount
01_01_05-planetary_gear
01_01_06-cylinder_screw_M4x10-DIN912 x 4
01_01_07-cylinder_screw_M6x16-DIN912 x 4
01_01_08-washer_M6-ISO7089 x 4
01_01_09-cylinder_screw_M5x25-DIN912 x 4
01_01_10-washer_M5-ISO7089 x 8
01_02_01-block
01_02_02-counterplate
01_02_03-milling_Cutter
01_02_04-hopper
deep groove ball bearing _01 x 2
deep groove ball bearing _02 x 2
deep groove ball bearing _03 x 2
deep groove ball bearing _04 x 2
deep groove ball bearing _05 x 2
deep groove ball bearing _06 x 2
deep groove ball bearing _07 x 2
deep groove ball bearing _08 x 2
deep groove ball bearing _09 x 2
deep groove ball bearing _10 x 2
deep groove ball bearing _11 x 2
deep groove ball bearing _12 x 2
deep groove ball bearing _13 x 2
deep groove ball bearing _14 x 2
01_02_06-bearing_Ring
01_02_07-sleeve_milling_cutter_gear
01_02_08-bearing_sleeve_1
01_02_09-bearing_sleeve_2
01_02_10-shredder_end_cap
01_02_11-clamping_flange
01_02_12-cylinder_screw_M5x10-DIN912 x 12
01_02_13-Cutter_head x 4
01_02_14-cylinder_screw_M4x12-DIN912 x 8
01_02_15-cylinder_screw_M5x80-DIN912 x 2
01_02_16-cylinder_screw_M5x100-DIN912 x 2
02_01_01-screw
02_01_02-tube_40-DN15
02_01_03-nozzle
02_01_04-worm_gear
02_02_00-tube_flange x 2
02_03_00-tube_100-DN15
02_04_00-hopper_extruder
02_05_00-cylinder_screw_M10x30-DIN912 x 4
02_06_00-nut_M10-DIN934 x 4
02_07_00-washer_M10-ISO7089 x 4
02_08_00-PTFE_insulation
03_00_00-profil_40x20_300
04_00_00-extruder_drawer
05_00_00-control_panel
06_00_00-profil_20x20_102_5
07_00_00-profil_20x20_104
08_00_00-fan_bracket

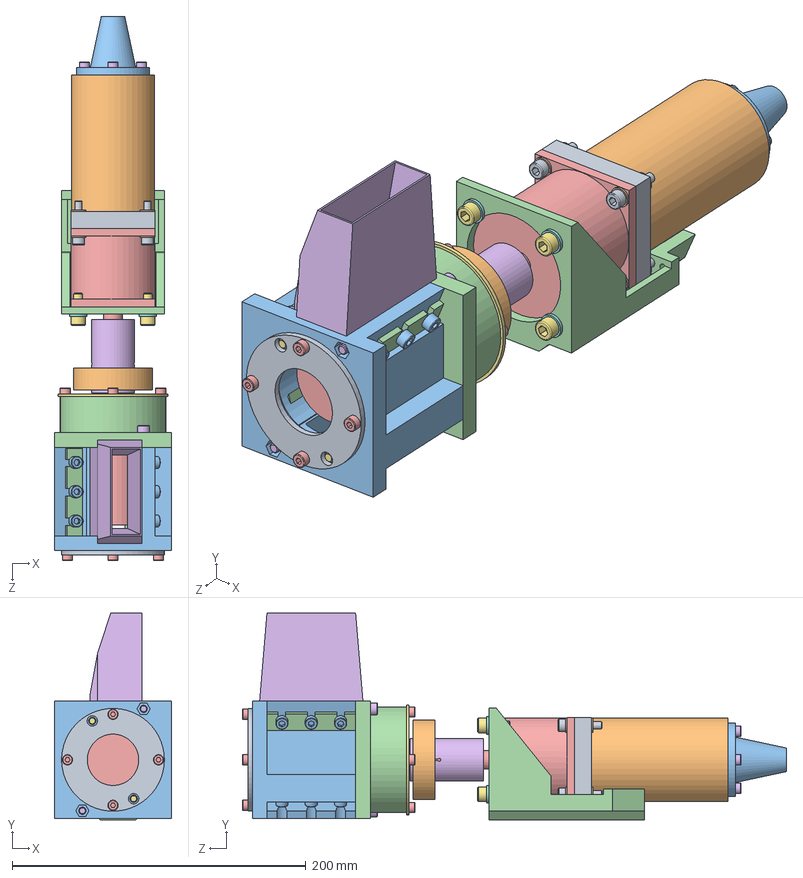
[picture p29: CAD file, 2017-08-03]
recycler/CAD/CAD(solidworks)/WeCycler/01_00_00-shredder_unit.SLDASM
80.0 x 141.0 x 370.9 mm
01_01_01-adapterplate_planetary_gear
01_01_02-engine
01_01_03-engine_end_cap
01_01_04-engine_mount
01_01_05-planetary_gear
01_01_06-cylinder_screw_M4x10-DIN912 x 4
01_01_07-cylinder_screw_M6x16-DIN912 x 4
01_01_08-washer_M6-ISO7089 x 4
01_01_09-cylinder_screw_M5x25-DIN912 x 4
01_01_10-washer_M5-ISO7089 x 8
01_02_01-block
01_02_02-counterplate
01_02_03-milling_Cutter
01_02_04-hopper
deep groove ball bearing _01 x 2
deep groove ball bearing _02 x 2
deep groove ball bearing _03 x 2
deep groove ball bearing _04 x 2
deep groove ball bearing _05 x 2
deep groove ball bearing _06 x 2
deep groove ball bearing _07 x 2
deep groove ball bearing _08 x 2
deep groove ball bearing _09 x 2
deep groove ball bearing _10 x 2
deep groove ball bearing _11 x 2
deep groove ball bearing _12 x 2
deep groove ball bearing _13 x 2
deep groove ball bearing _14 x 2
01_02_06-bearing_Ring
01_02_07-sleeve_milling_cutter_gear
01_02_08-bearing_sleeve_1
01_02_09-bearing_sleeve_2
01_02_10-shredder_end_cap
01_02_11-clamping_flange
01_02_12-cylinder_screw_M5x10-DIN912 x 12
01_02_13-Cutter_head x 4
01_02_14-cylinder_screw_M4x12-DIN912 x 8
01_02_15-cylinder_screw_M5x80-DIN912 x 2
01_02_16-cylinder_screw_M5x100-DIN912 x 2

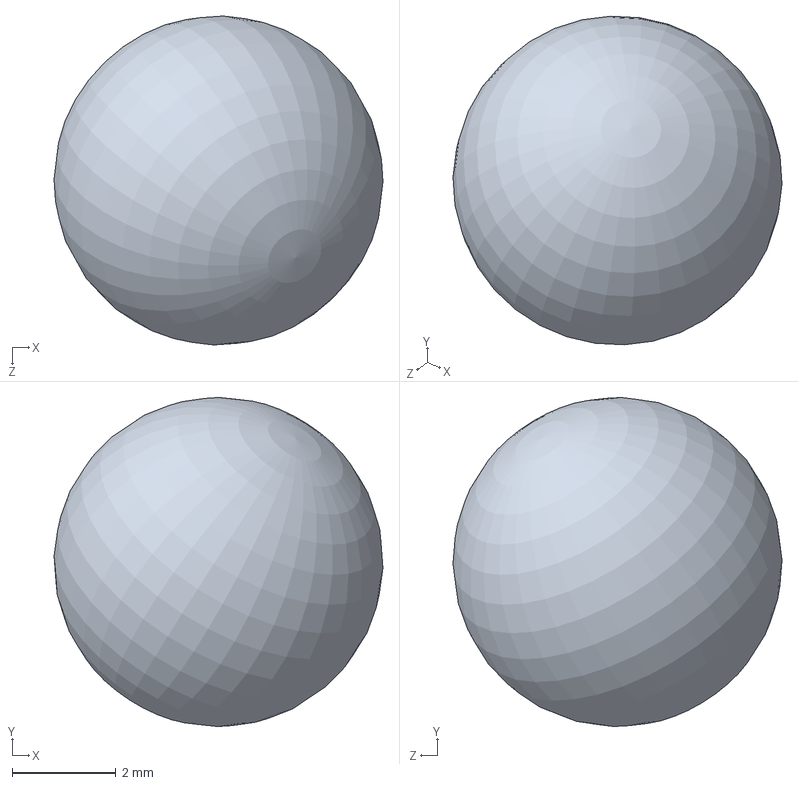
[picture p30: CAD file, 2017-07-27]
recycler/CAD/CAD(solidworks)/shredder_unit/deep groove ball bearing _09.SLDPRT
6.35 x 6.35 x 6.35 mm

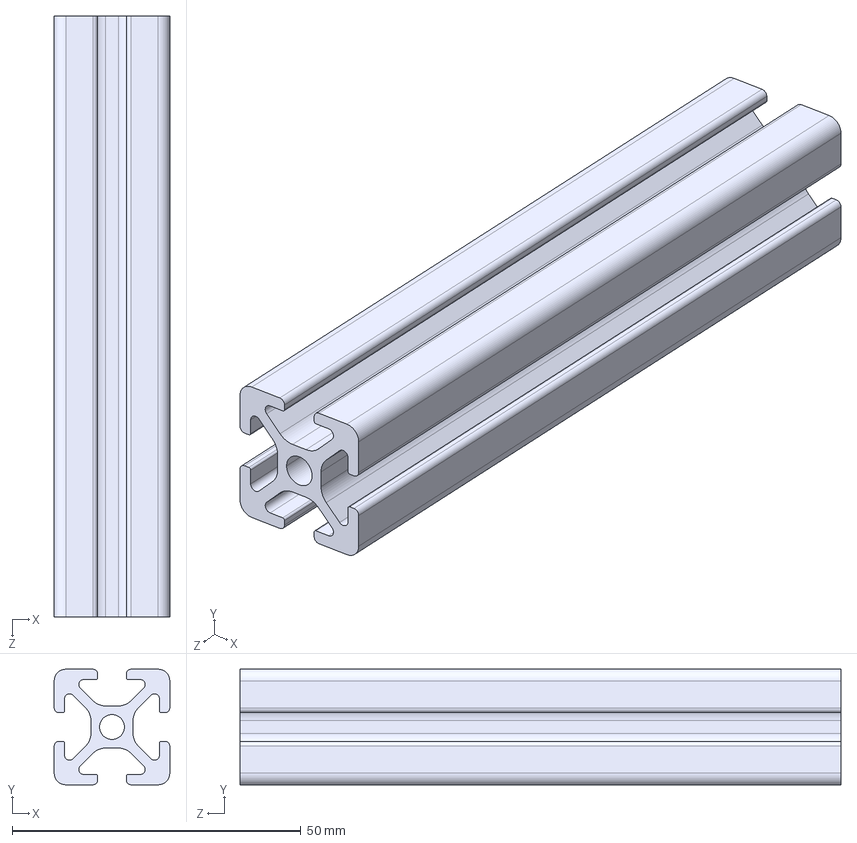
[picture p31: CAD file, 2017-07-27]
recycler/CAD/CAD(step)/07_00_00-profil_20x20_104.STEP
20.0 x 20.0 x 104.0 mm

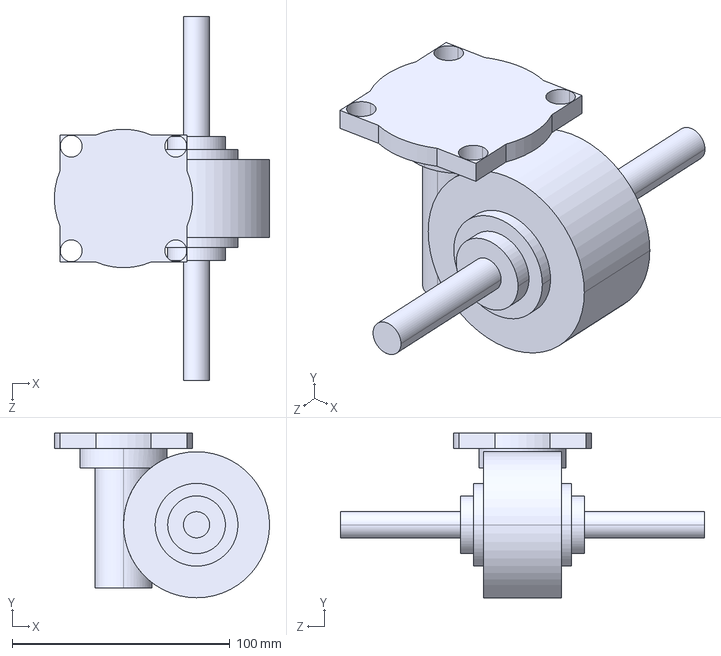
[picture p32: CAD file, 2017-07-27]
recycler/CAD/CAD(step)/extruder_unit/02_01_04-worm_gear.step
98.7 x 75.5 x 167.0 mm

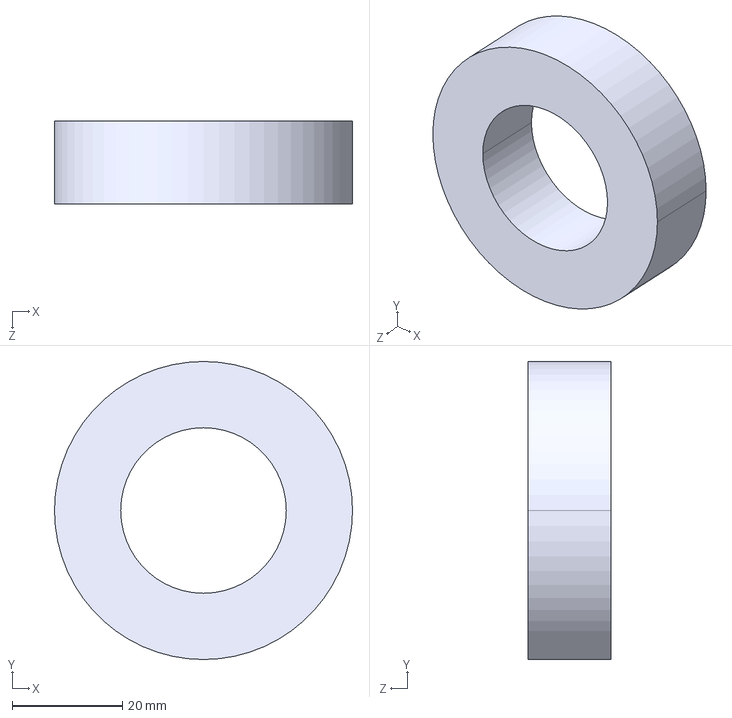
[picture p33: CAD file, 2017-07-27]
recycler/CAD/CAD(step)/shredder_unit/cutting_unit/01_02_11-clamping_flange.step
54.0 x 54.0 x 15.0 mm

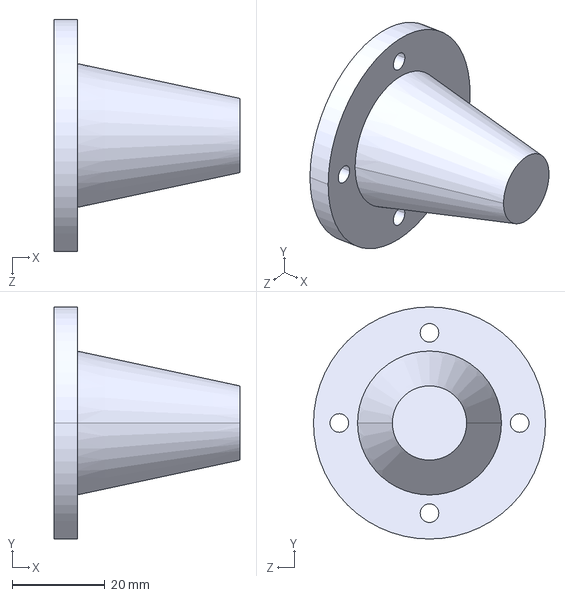
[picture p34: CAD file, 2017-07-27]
recycler/CAD/CAD(step)/shredder_unit/powertrain_unit/01_01_03-engine_end_cap.step
40.0 x 50.0 x 50.0 mm

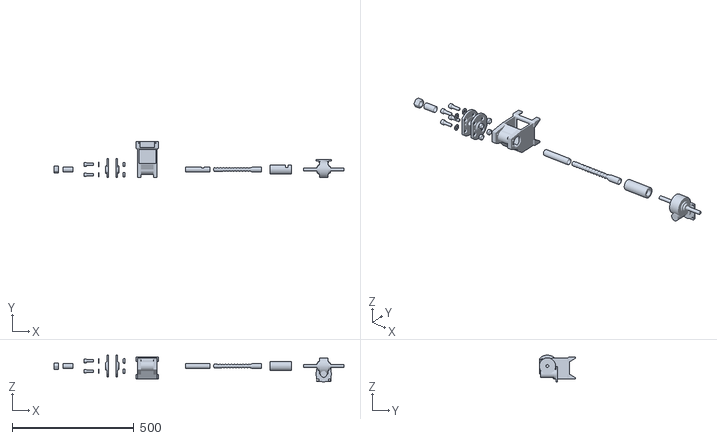
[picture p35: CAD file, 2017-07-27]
recycler/CAD/CAD(stl)/extruder_unit/02_00_00-extruder_unit(explosion).STL
1192.4 x 149.7 x 110.2

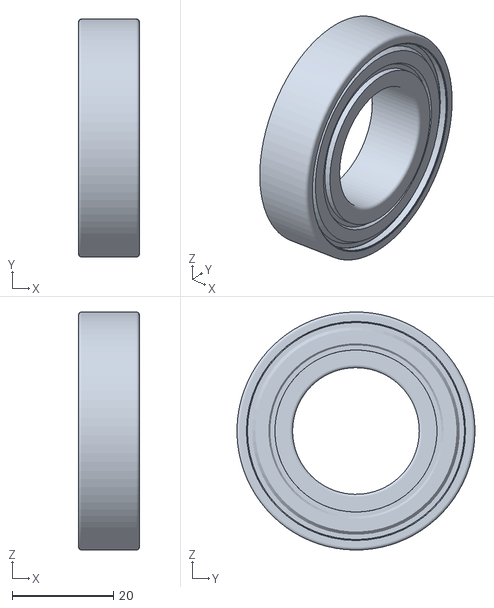
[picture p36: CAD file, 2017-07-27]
recycler/CAD/CAD(stl)/shredder_unit/cutting_unit/01_02_05-deep_groove_ball_bearing_FAG6005_2Z-DIN625.STL
12.0 x 47.0 x 47.0

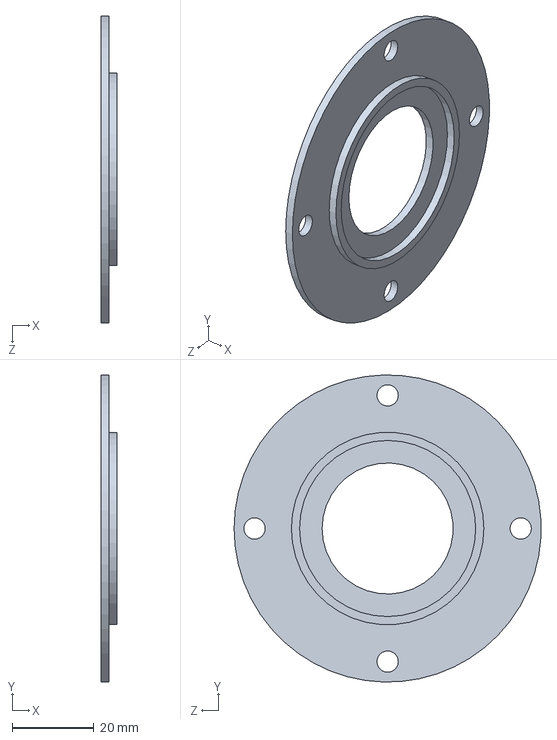
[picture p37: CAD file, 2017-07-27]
recycler/CAD/CAD(solidworks)/shredder_unit/01_02_08-bearing_sleeve_1.SLDPRT
4.00 x 75.0 x 74.9 mm

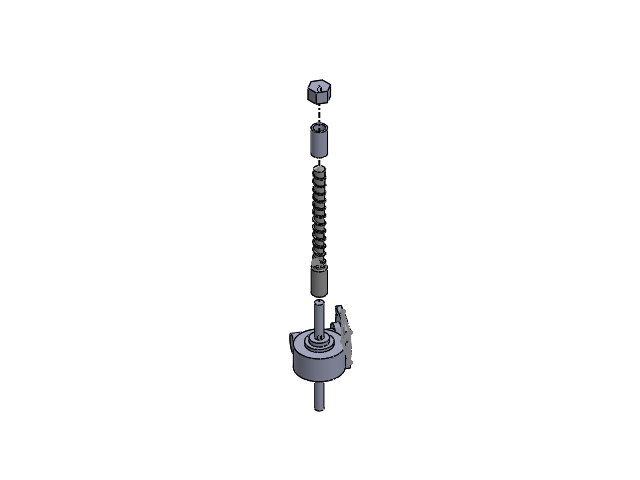
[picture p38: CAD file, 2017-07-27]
recycler/CAD/CAD(solidworks)/extruder_unit/02_01_00-extruder.SLDASM
02_01_01-screw
02_01_02-tube_40-DN15
02_01_03-nozzle
02_01_04-worm_gear

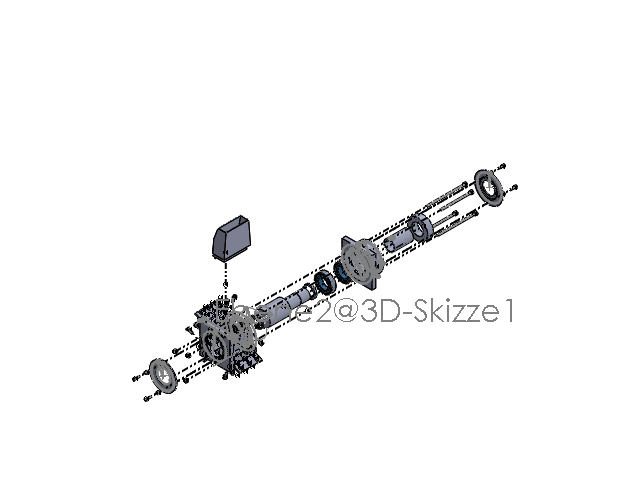
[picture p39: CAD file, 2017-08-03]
recycler/CAD/CAD(solidworks)/WeCycler/01_02_00-cutting_unit.SLDASM
01_02_01-block
01_02_02-counterplate
01_02_03-milling_Cutter
01_02_04-hopper
deep groove ball bearing _01 x 2
deep groove ball bearing _02 x 2
deep groove ball bearing _03 x 2
deep groove ball bearing _04 x 2
deep groove ball bearing _05 x 2
deep groove ball bearing _06 x 2
deep groove ball bearing _07 x 2
deep groove ball bearing _08 x 2
deep groove ball bearing _09 x 2
deep groove ball bearing _10 x 2
deep groove ball bearing _11 x 2
deep groove ball bearing _12 x 2
deep groove ball bearing _13 x 2
deep groove ball bearing _14 x 2
01_02_06-bearing_Ring
01_02_07-sleeve_milling_cutter_gear
01_02_08-bearing_sleeve_1
01_02_09-bearing_sleeve_2
01_02_10-shredder_end_cap
01_02_11-clamping_flange
01_02_12-cylinder_screw_M5x10-DIN912 x 12
01_02_13-Cutter_head x 4
01_02_14-cylinder_screw_M4x12-DIN912 x 8
01_02_15-cylinder_screw_M5x80-DIN912 x 2
01_02_16-cylinder_screw_M5x100-DIN912 x 2
01_02_17-nut_M5-DIN934 x 4

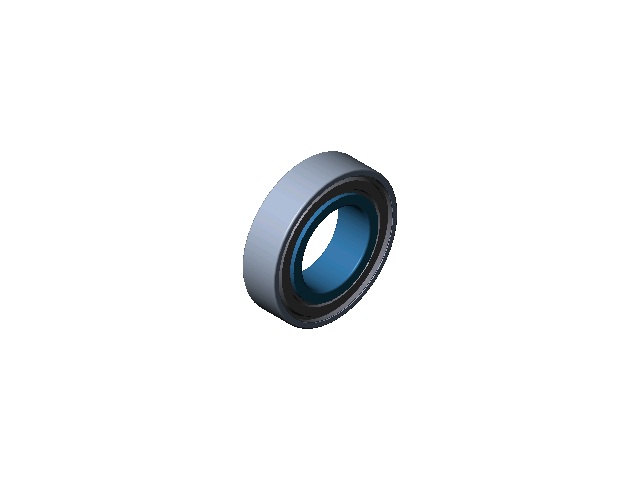
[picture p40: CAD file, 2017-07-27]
recycler/CAD/CAD(solidworks)/shredder_unit/01_02_05-deep_groove_ball_bearing_FAG6005_2Z-DIN625-1.SLDASM
deep groove ball bearing _01
deep groove ball bearing _02
deep groove ball bearing _03
deep groove ball bearing _04
deep groove ball bearing _05
deep groove ball bearing _06
deep groove ball bearing _07
deep groove ball bearing _08
deep groove ball bearing _09
deep groove ball bearing _10
deep groove ball bearing _11
deep groove ball bearing _12
deep groove ball bearing _13
deep groove ball bearing _14

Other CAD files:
recycler/CAD/CAD(solidworks)/WeCycler/01_01_00-powertrain_unit.SLDASM
recycler/CAD/CAD(solidworks)/WeCycler/02_01_00-extruder.SLDASM
recycler/CAD/CAD(step)/shredder_unit/01_00_00-shredder_unit.STEP
recycler/CAD/CAD(solidworks)/00_00_00-wecycler(explosion).SLDDRW
recycler/CAD/CAD(solidworks)/01_00_00-shredder_unit(explosion).SLDDRW
recycler/CAD/CAD(solidworks)/01_01_00-powertrain_unit(explosion).SLDDRW
recycler/CAD/CAD(solidworks)/01_02_00-cutting_unit(explosion).SLDDRW
recycler/CAD/CAD(solidworks)/02_00_00-extruder_unit(explosion).SLDDRW
recycler/CAD/CAD(solidworks)/WeCycler/03_00_00-profil_40x20_300.SLDPRT
recycler/CAD/CAD(solidworks)/WeCycler/04_00_00-extruder_drawer.SLDPRT
recycler/CAD/CAD(solidworks)/WeCycler/05_00_00-control_panel.SLDPRT
recycler/CAD/CAD(solidworks)/WeCycler/06_00_00-profil_20x20_102_5.SLDPRT
recycler/CAD/CAD(solidworks)/WeCycler/07_00_00-profil_20x20_104.SLDPRT
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

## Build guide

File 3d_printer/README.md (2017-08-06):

# 3D Printer 

Prusai3

For the CubeFactory2 project an open source printer from RepRap was used. The decision for selecting this printer was made by the decisive facts of the dimensions and the price.

The Hephestos is a further development of the Prusa i3 by RepRap. It offers significant improvements and consists of a DIY (do it yourself) assembly set that is easier and more intuitive. Hephestos offers to create designs, prototypes, figures, accessories, models, etc.
This model is characterized by its easy and convenient assembly. As a result, the individual steps were substantially simplified and the instructions were made more visual. The Hephestos is based 100% on free hardware and can be changed and further developed.

Here are some facts about the 3D printer and links to the shop, where you can buy it:

### BQ – Prusa I3
  - Print volume: 215 x 210 x 180 mm
  - Outer dimensions: 460 x 383 x 430 mm
  - Performance: 100 W
  - Weight: 9,7 kg
  - Price: 549,9 €
  - License: Creative Commons – Attribution – Share Alike
  - GitHub: https://github.com/bq/prusa-i3-hephestos 

#### Shops and prices:
- 3d printer: 549,90 €
https://www.bq.com/de/hephestos-prusa
https://www.comprise.de/3d-drucker-bq-hephestos/a-33169/
- MK2a Heated Bed Kit: 19,90 €
https://www.comprise.de/mk2a-heated-bed-kit/a-46306/
- Printer Bed Sheet BuildTak 215 x 240 mm: 21,90 €
https://www.comprise.de/druckbettfolie-buildtak-215-x-240-mm/a-32599/
- Printer Bed Sheet BuildTak 225 x 254 mm: 21,90 €
https://www.comprise.de/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
- ##### Total price: 613,60 €
#### Downloads: 
https://www.bq.com/de/support/hephestos/support-sheet

For those, who don’t have restrictions on the printer size and price, or just want to have a look at the original hardware, here are the links:

- Prusa i3 – published under GPL v3 - first version: https://github.com/josefprusa/Prusa3-vanilla 
- Prusa i3 MK2S 3D Printer – new Version: https://github.com/prusa3d/Original-Prusa-i3 
http://www.prusa3d.com/

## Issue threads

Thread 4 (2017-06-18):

Wie kann man Dateien mit github Desktop ändern/verschieben/ordnen? - Ein Vorschlag

karlamitk, 2017-06-18:
# github Desktop benutzen
## Projekt einrichten
- Github Desktop installieren.
- Persönl. Einstellungen (File > Options):
    - Zugangsdaten zu github (Accoun"ts)
    - Daten, mit denen alles unterschrieben wird (Git)
- Unser Projekt herunterladen:
    - (File > Clone Repository)
    - URL: patmu04/cubefactory
    - local path: Ordner, wo das Projekt liegen soll
- Projekt ist eingerichtet

## Workflow (Änderungen machen)
### Unser Workflow grob zusammengefasst
- neuen Branch für die Änderungen anlegen (Branch > New Branch, Namen geben)
- darauf achten, dass oben bei "current branch" der neue Branchname steht
    - beliebig Änderungen an den Dokumenten /der Ordnerstruktur im Projektordner unter local path vornehmen
    - dabei tauchen in Git Desktop rote und blaue Zeilen mit den Änderungen auf. Links sind die changed files (Verschieben ist auch eine Änderung (des Dateinamens) auf)
    -wenn genug geändert, commit machen
    -dazu unten links Beschreibung der Änderungen (kurz, dort wo summary steht) eintippen und click auf commit to <mein branchname>
- so viele commits machen, wie gewünscht
- um ins remote repository (das, was man auf der Homepage sieht) zu pushen (hochladen/veröffentlichen):
    - oben, wo meist "fetch origin" steht auf den "Push to origin" Button klicken
    - erscheint online (allerdings nur, wenn man den branch von master auf den eigenen branchnamen ändert
    - schnellster Weg dorthin: (Repository > View on Github)
    - zusammenführen geht über pull request

### Links zum Workflow
- Workflow zusammengefasst (Links beziehen sich nicht auf github desktop)
    - https://guides.github.com/activities/hello-world/
    - https://help.github.com/articles/github-flow/
    -  https://guides.github.com/introduction/flow/
-  Video, was ungefähr dem entspricht, was WIR machen, allerdings clone repository (siehe oben) anstatt add existing"
    - https://www.youtube.com/watch?v=ISkPyNkM2iY

## Git allgemein verstehen
- sehr ausführlich: https://git-scm.com/book/en/v2
- kürzer https://homepages.thm.de/~hg11260/mat/git.pdf
    - v.a. die ersten 2 Seiten können helfen für ein Grundverständnis
    - Beispiel nutzt nur Kommandozeile und andere Plattform (kein github)# github Desktop benutzen

karlamitk, 2017-06-18:
siehe auch [ https://github.com/karlamitk/testrep/Anleitung_Github_Desktop.md  ](url)

Closed 2017-11-29.

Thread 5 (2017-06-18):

Wie formatiere ich mein README? - Ein paar Links und Beispiele

karlamitk, 2017-06-18:
Guckst du hier:https://github.com/karlamitk/testrep/blob/master/Anleitungen/Anleitung_Markdown.md

patmu04, 2017-07-07:
der Markdown Editor, den Karla heute kurz gezeigt hat:
http://dillinger.io/
dort kann man recht praktisch nebeneinander in markdown schreiben und rechts direkt die Vorschau sehen

jbon, 2017-07-08:
ich benutze den Editor namens "texts" http://www.texts.io/

karlamitk, 2017-07-14:
ich hab die Anleitung für Links innerhalb des Dokuments berichtigt.

Closed 2017-11-29.

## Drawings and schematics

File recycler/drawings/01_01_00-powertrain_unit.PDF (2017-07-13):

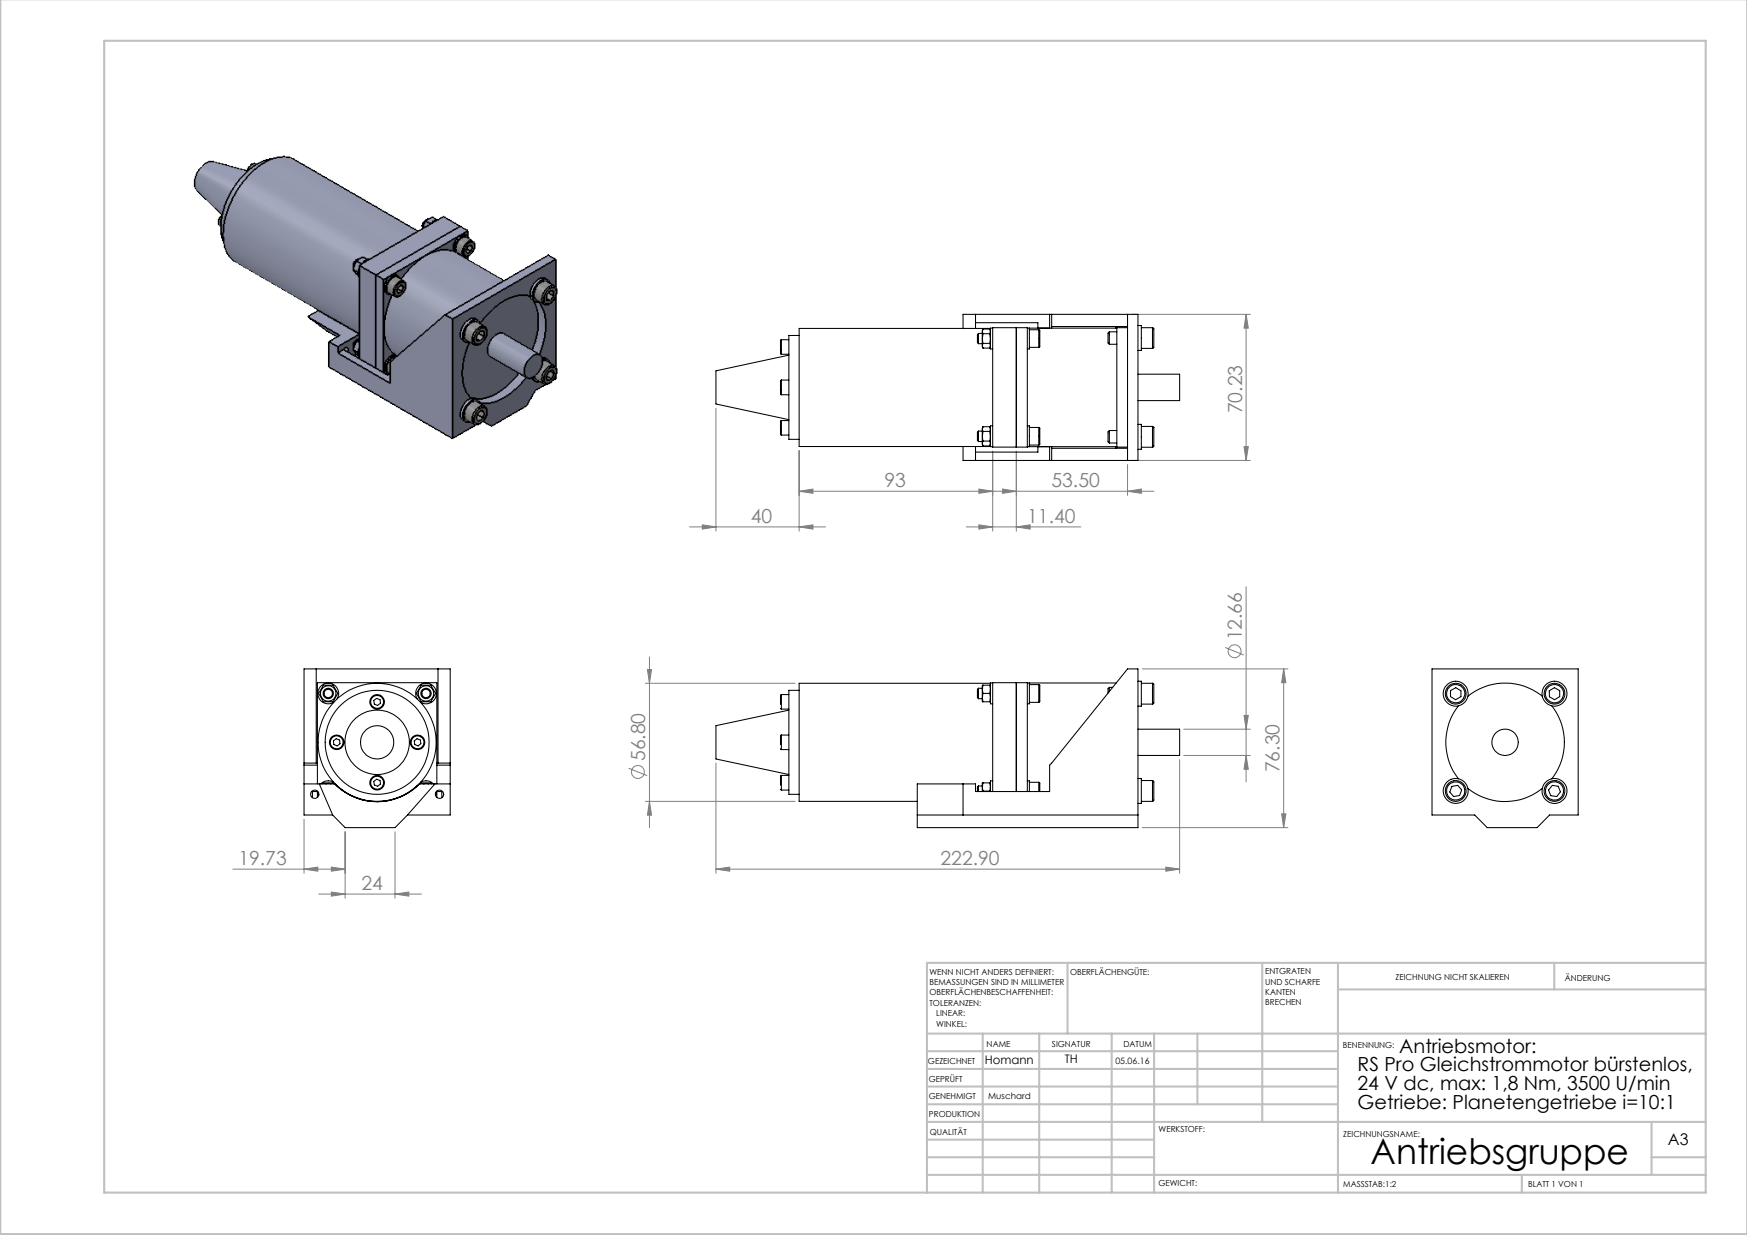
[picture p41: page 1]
MASSSTAB:1:2; BLATT 1 VON 1; ZEICHNUNG NICHT SKALIEREN; ÄNDERUNG; UND SCHARFE; WENN NICHT ANDERS DEFINIERT:; OBERFLÄCHENGÜTE:

BEMASSUNGEN SIND IN MILLIMETER
OBERFLÄCHENBESCHAFFENHEIT:
TOLERANZEN:
LINEAR:
WINKEL:

NAME | SIGNATUR | DATUM | | | | Antriebsmotor: BENENNUNG: RS Pro Gleichstrommotor bürstenlos, 24 V dc, max: 1,8 Nm, 3500 U/min Getriebe: Planetengetriebe i=10:1
QUALITÄT | | | | WERKSTOFF: | ZEICHNUNGSNAME: Antriebsgruppe GEWICHT: | A3

GEZEICHNET | Homann | TH | 05.06.16

GEPRÜFT
GENEHMIGT | Muschard
PRODUKTION

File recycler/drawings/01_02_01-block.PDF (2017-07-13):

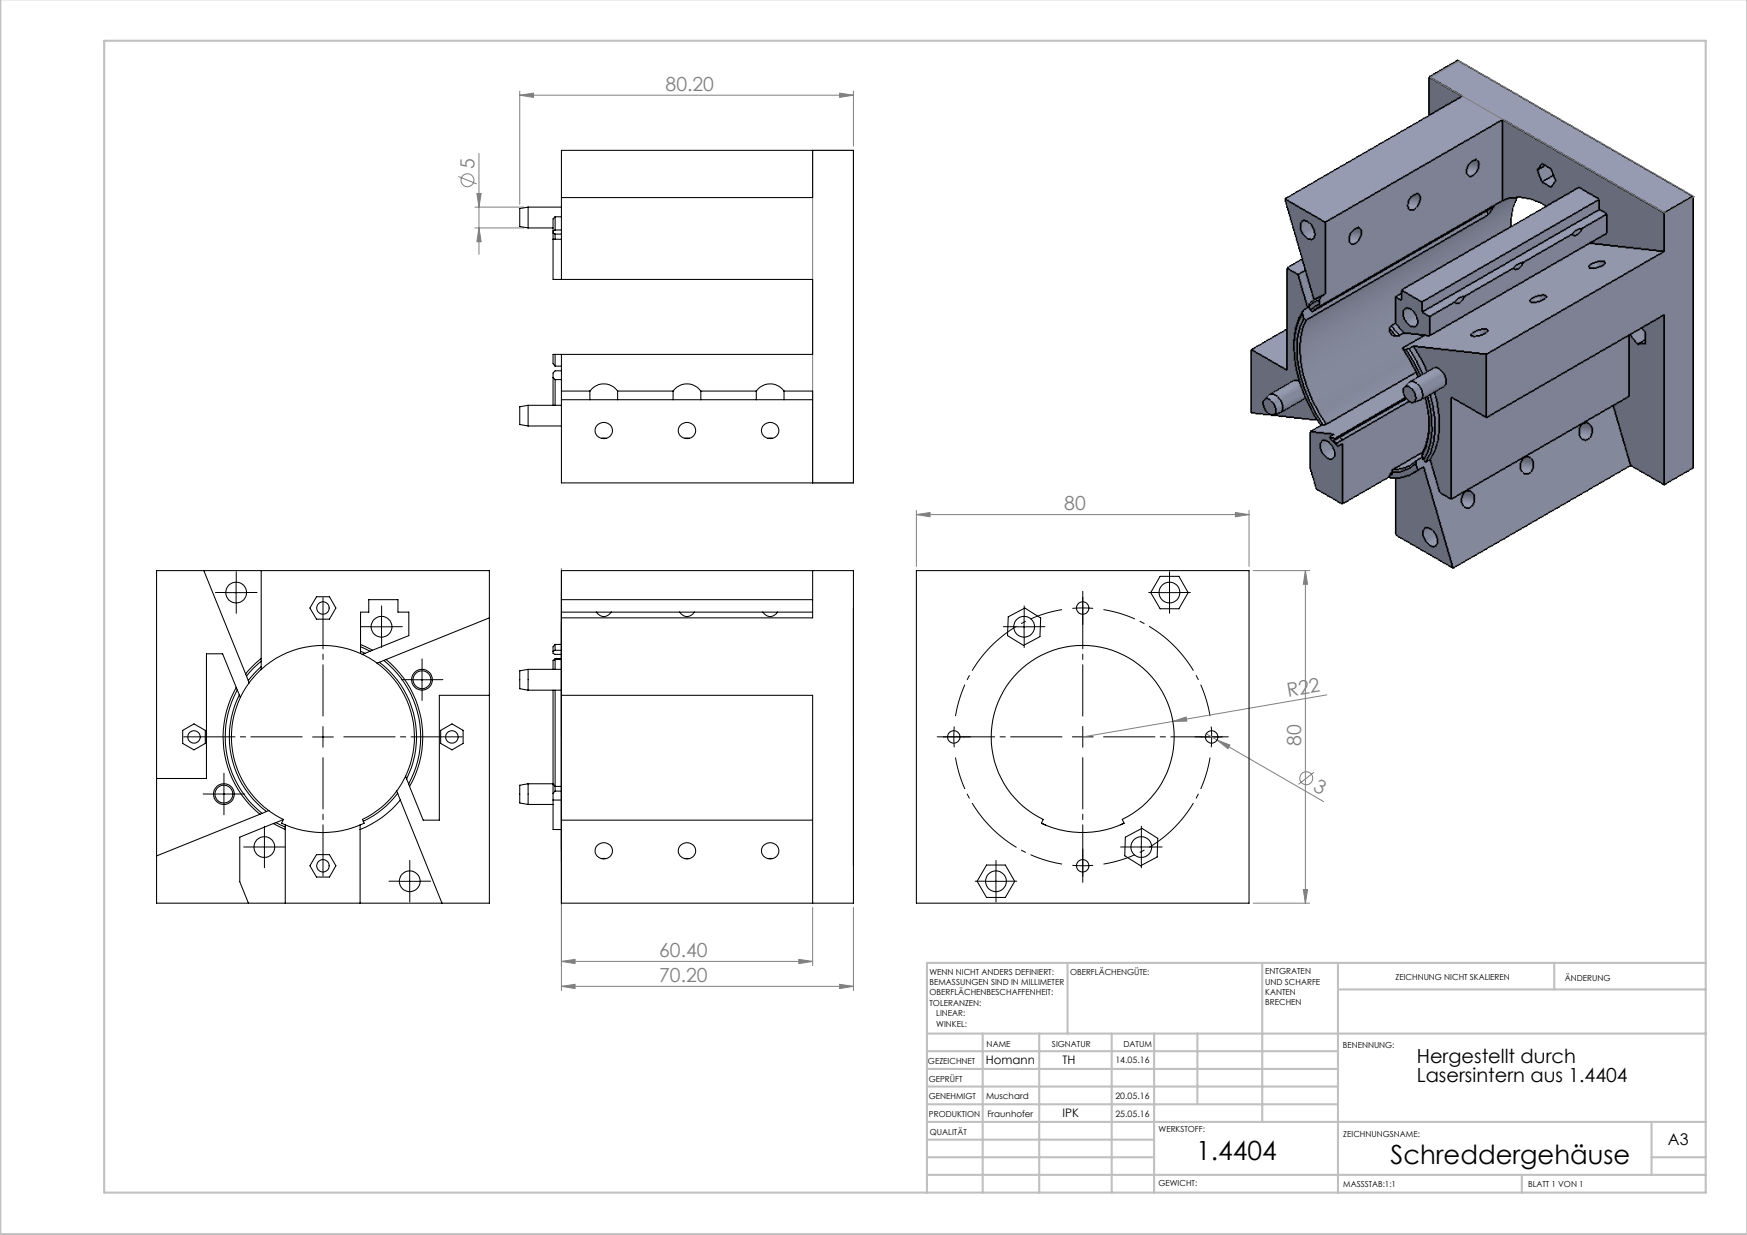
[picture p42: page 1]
MASSSTAB:1:1; BLATT 1 VON 1; ZEICHNUNG NICHT SKALIEREN; ÄNDERUNG; UND SCHARFE; WENN NICHT ANDERS DEFINIERT:; OBERFLÄCHENGÜTE:

BEMASSUNGEN SIND IN MILLIMETER
OBERFLÄCHENBESCHAFFENHEIT:
TOLERANZEN:
LINEAR:
WINKEL:

NAME | SIGNATUR TH | DATUM | | | | BENENNUNG: Hergestellt durch Lasersintern aus 1.4404

GEZEICHNET | Homann | | 14.05.16

GEPRÜFT
GENEHMIGT | Muschard | | 20.05.16
PRODUKTION | Fraunhofer | IPK | 25.05.16
QUALITÄT | | | | WERKSTOFF: 1.4404 | ZEICHNUNGSNAME: Schreddergehäuse GEWICHT: | A3

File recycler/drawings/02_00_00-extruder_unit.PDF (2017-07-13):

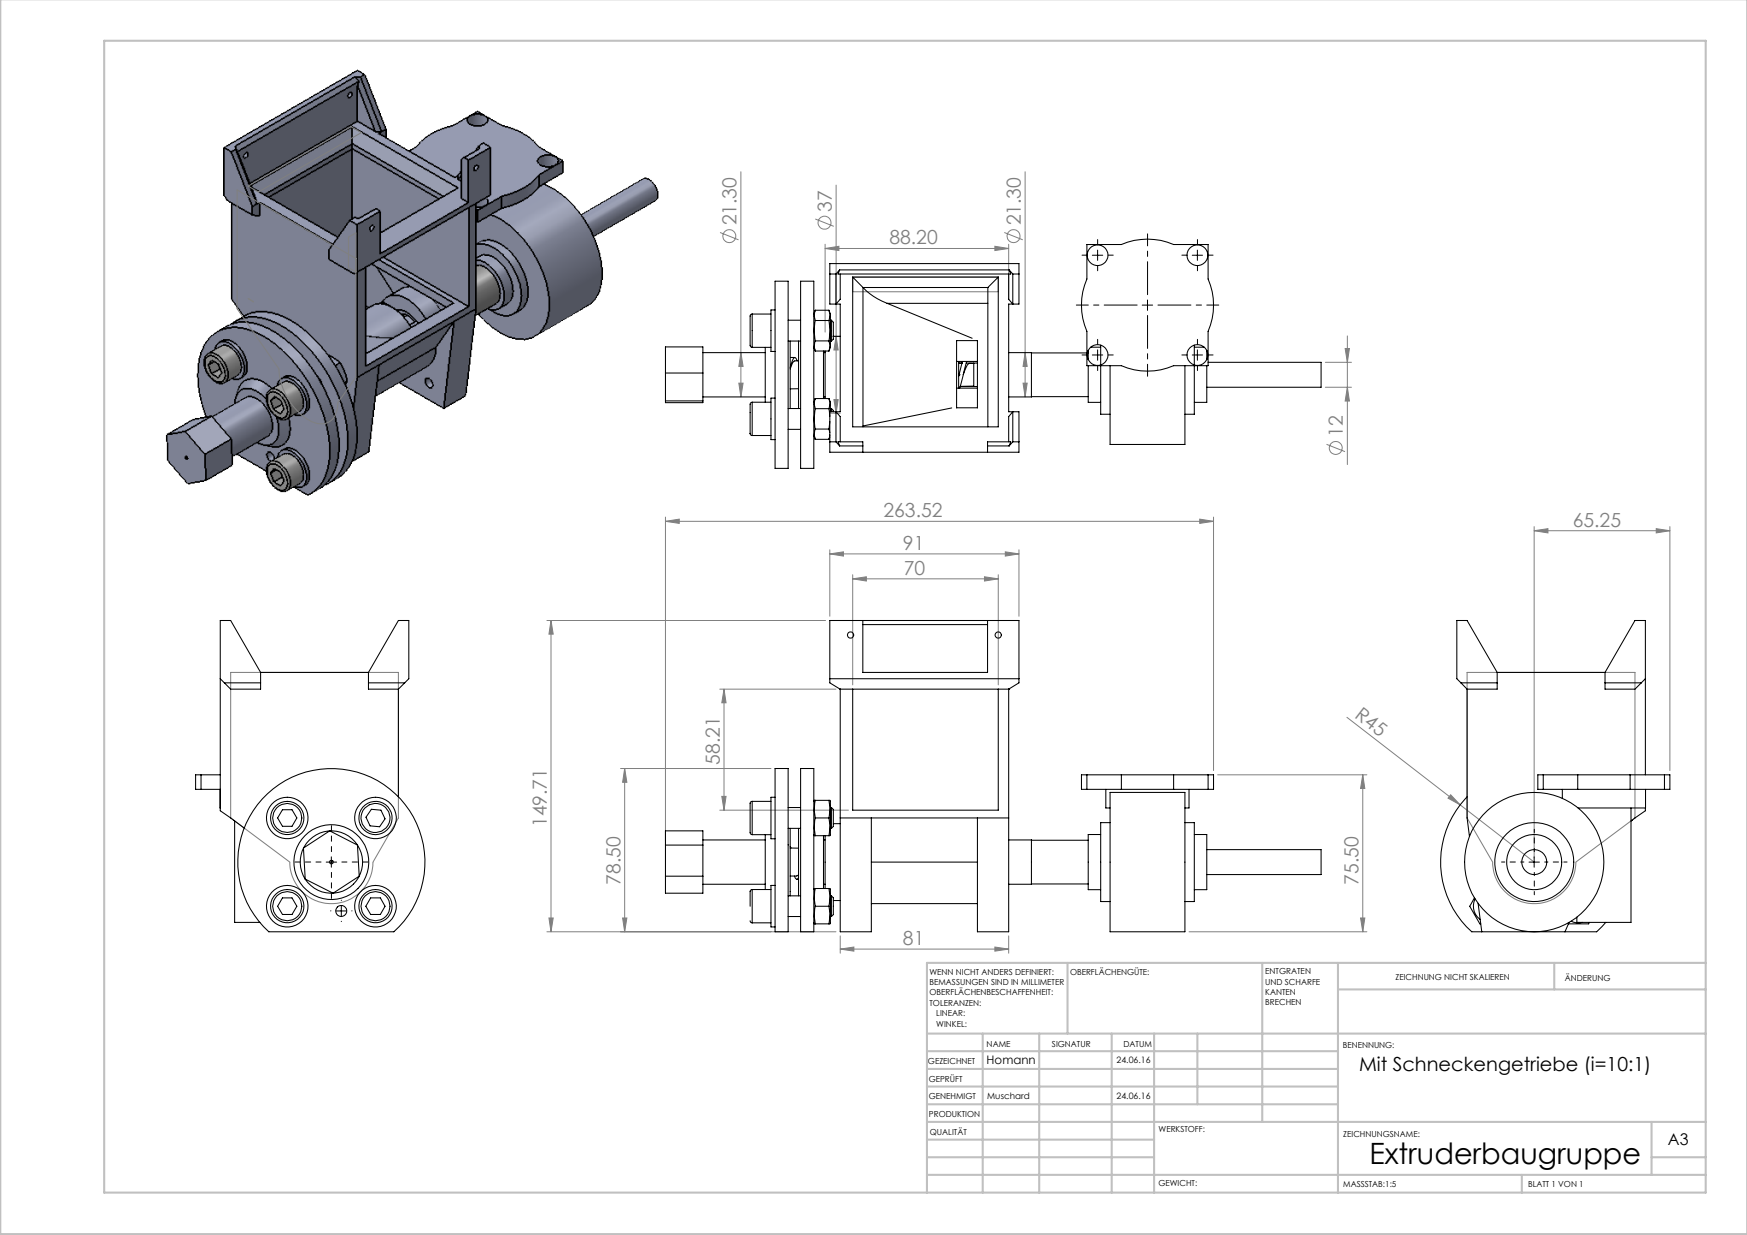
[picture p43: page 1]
MASSSTAB:1:5; BLATT 1 VON 1; ZEICHNUNG NICHT SKALIEREN; ÄNDERUNG; UND SCHARFE; WENN NICHT ANDERS DEFINIERT:; OBERFLÄCHENGÜTE:

BEMASSUNGEN SIND IN MILLIMETER
OBERFLÄCHENBESCHAFFENHEIT:
TOLERANZEN:
LINEAR:
WINKEL:

NAME | SIGNATUR | DATUM | | | | BENENNUNG: Mit Schneckengetriebe (i=10:1)

GEZEICHNET | Homann | | 24.06.16
QUALITÄT | | | | WERKSTOFF: | ZEICHNUNGSNAME: Extruderbaugruppe GEWICHT: | A3

GEPRÜFT
GENEHMIGT | Muschard | | 24.06.16
PRODUKTION

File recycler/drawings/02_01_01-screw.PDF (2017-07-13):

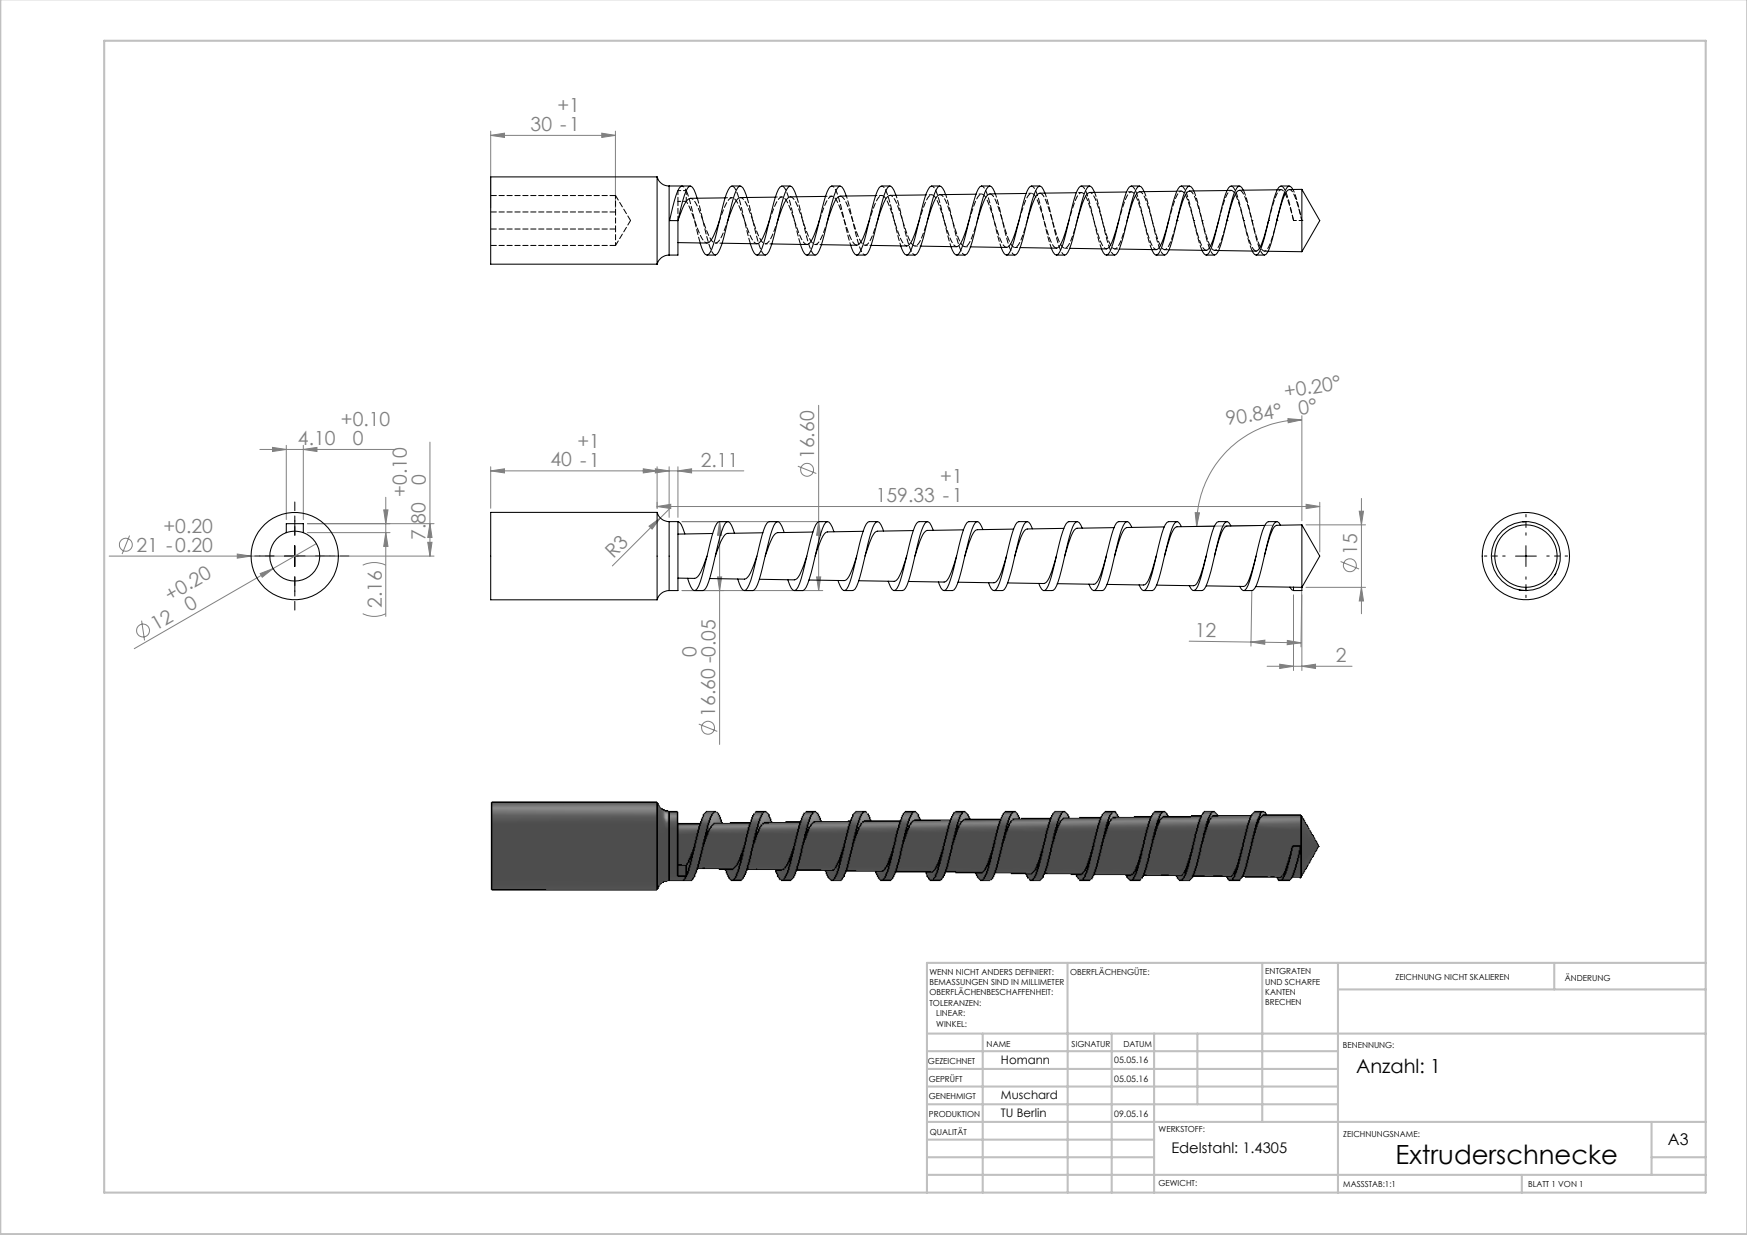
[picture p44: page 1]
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

BEMASSUNGEN SIND IN MILLIMETER
OBERFLÄCHENBESCHAFFENHEIT:
TOLERANZEN:
LINEAR:
WINKEL:

NAME | SIGNATUR | DATUM | | | | BENENNUNG: Anzahl: 1

GEZEICHNET | Homann | | 05.05.16
GEPRÜFT | | | 05.05.16
GENEHMIGT | Muschard
PRODUKTION | TU Berlin | | 09.05.16
QUALITÄT | | | | WERKSTOFF: Edelstahl: 1.4305 | ZEICHNUNGSNAME: Extruderschnecke GEWICHT: | A3

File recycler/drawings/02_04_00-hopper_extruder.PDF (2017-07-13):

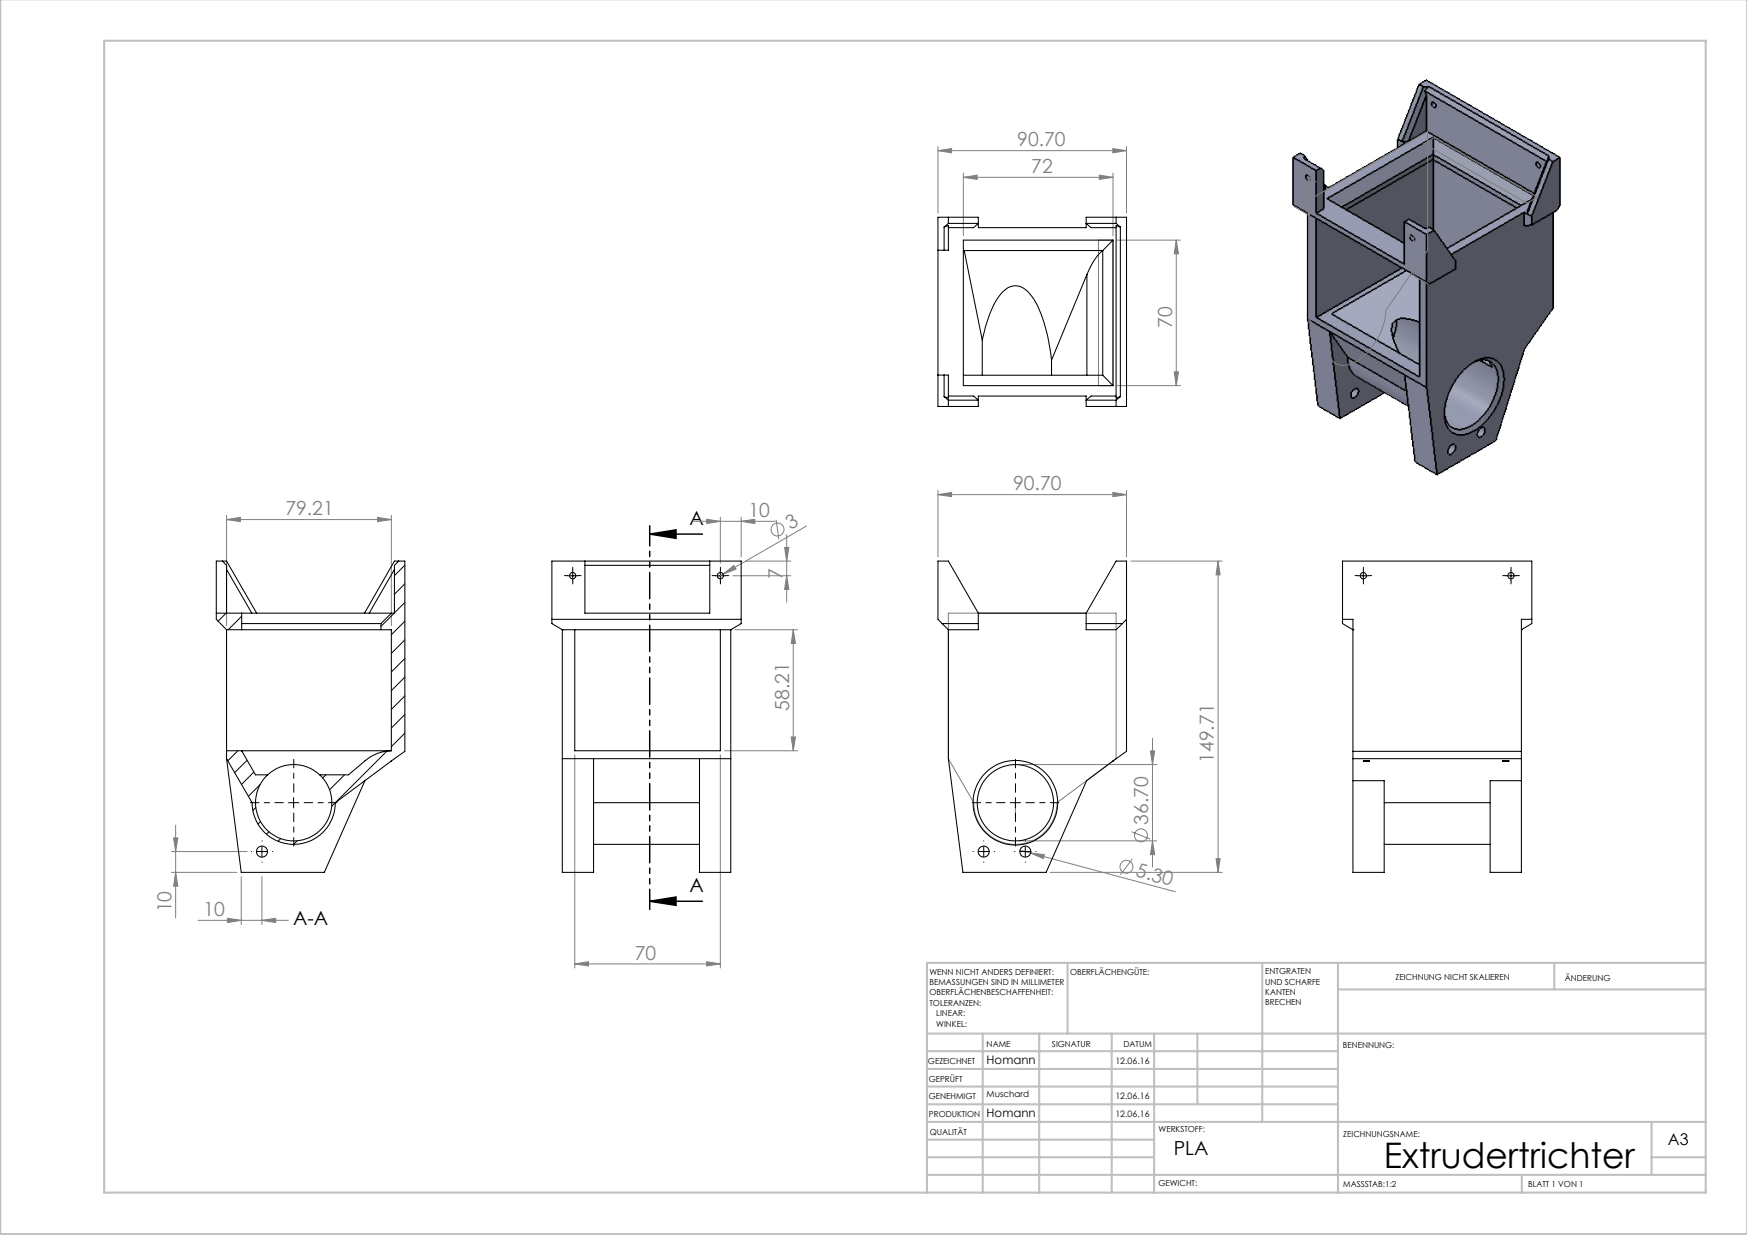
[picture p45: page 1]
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

BEMASSUNGEN SIND IN MILLIMETER
OBERFLÄCHENBESCHAFFENHEIT:
TOLERANZEN:
LINEAR:
WINKEL:

NAME | SIGNATUR | DATUM | | | | BENENNUNG:
QUALITÄT | | | | WERKSTOFF: PLA | ZEICHNUNGSNAME: Extrudertrichter GEWICHT: | A3

GEZEICHNET | Homann | | 12.06.16

GEPRÜFT
GENEHMIGT | Muschard | | 12.06.16
PRODUKTION | Homann | | 12.06.16

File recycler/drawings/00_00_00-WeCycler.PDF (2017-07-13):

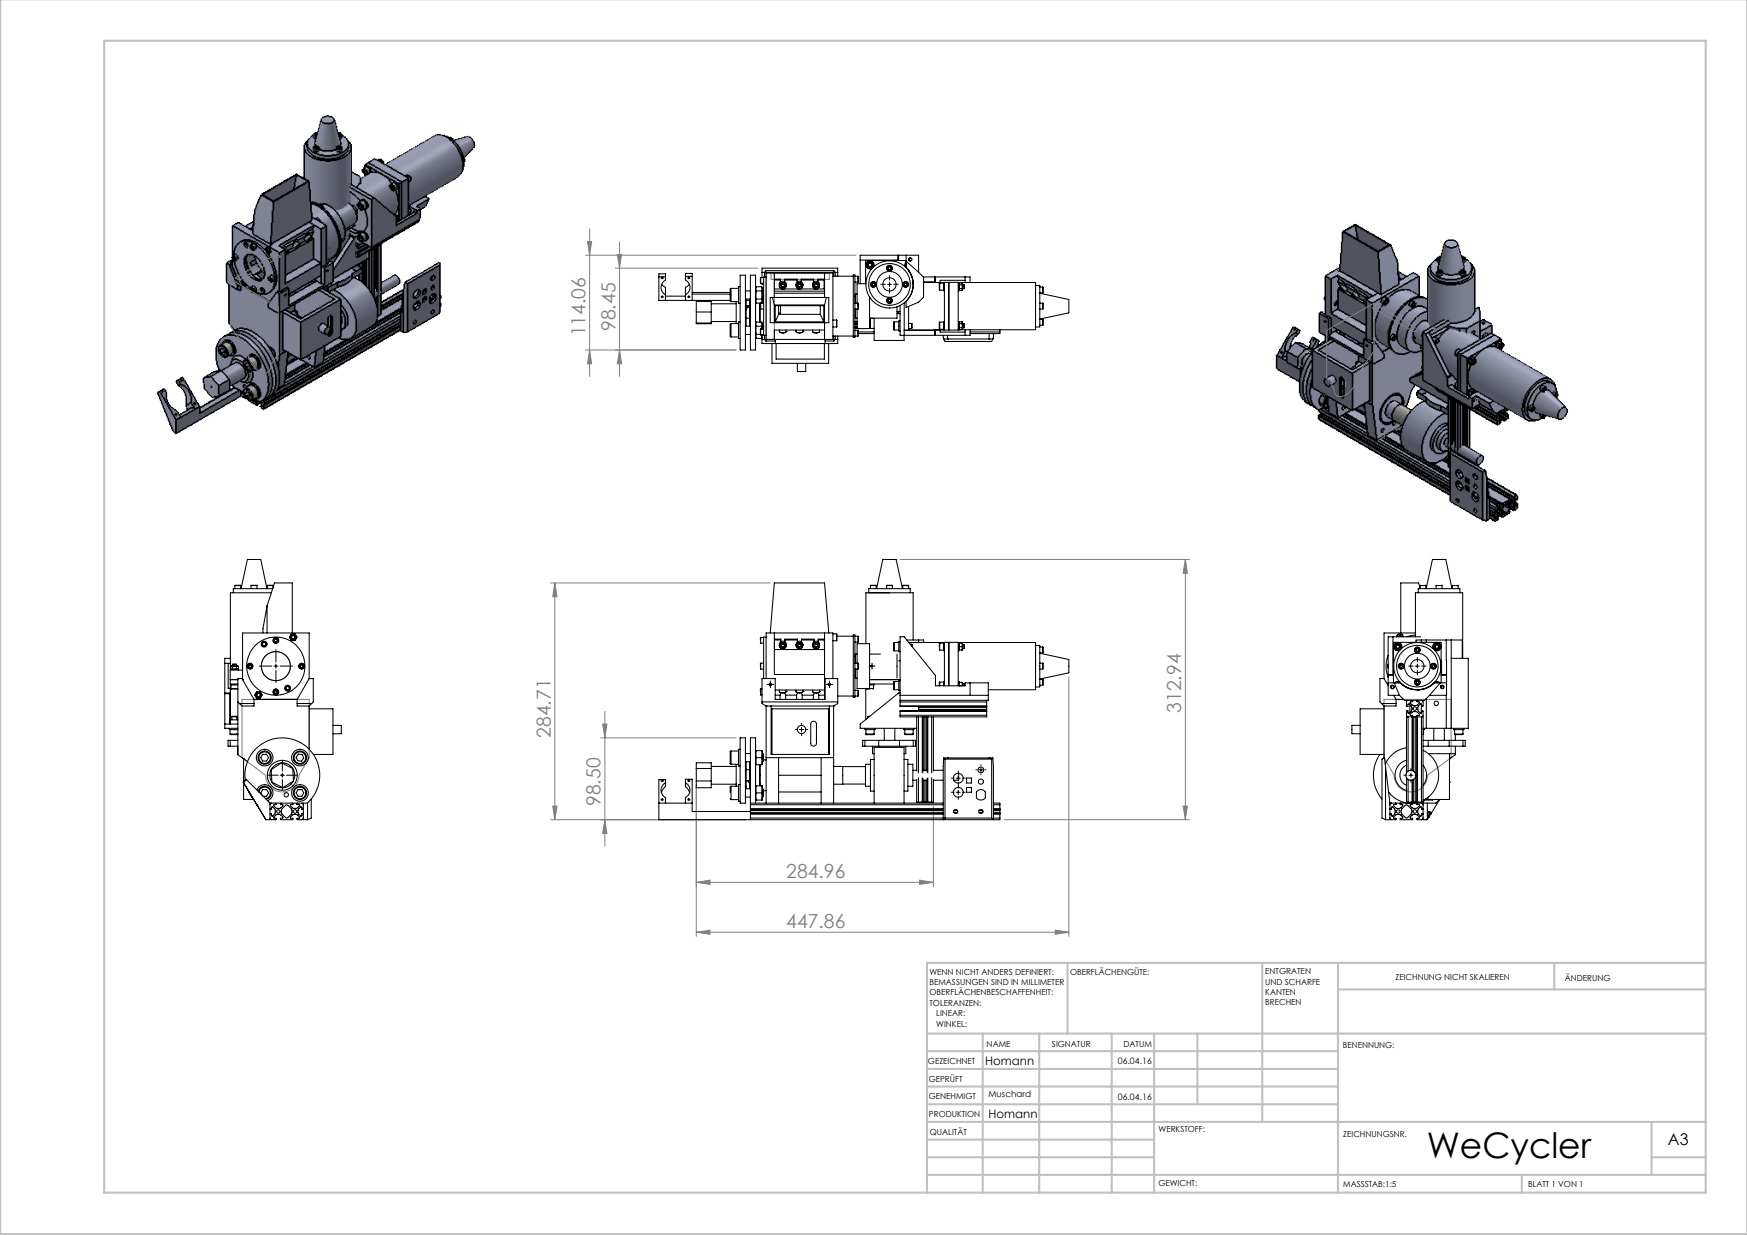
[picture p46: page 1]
GEZEICHNET Homann; MASSSTAB:1:5; BLATT 1 VON 1; ZEICHNUNG NICHT SKALIEREN; ÄNDERUNG; UND SCHARFE; WENN NICHT ANDERS DEFINIERT:; OBERFLÄCHENGÜTE:

BEMASSUNGEN SIND IN MILLIMETER
OBERFLÄCHENBESCHAFFENHEIT:
TOLERANZEN:
LINEAR:
WINKEL:

NAME | SIGNATUR | DATUM | | | | BENENNUNG:
QUALITÄT | | | | WERKSTOFF: | WeCycler GEWICHT: ZEICHNUNGSNR. | A3

GEZEICHNET | Homann
GEPRÜFT
GENEHMIGT | Muschard | | 06.04.16
PRODUKTION | Homann

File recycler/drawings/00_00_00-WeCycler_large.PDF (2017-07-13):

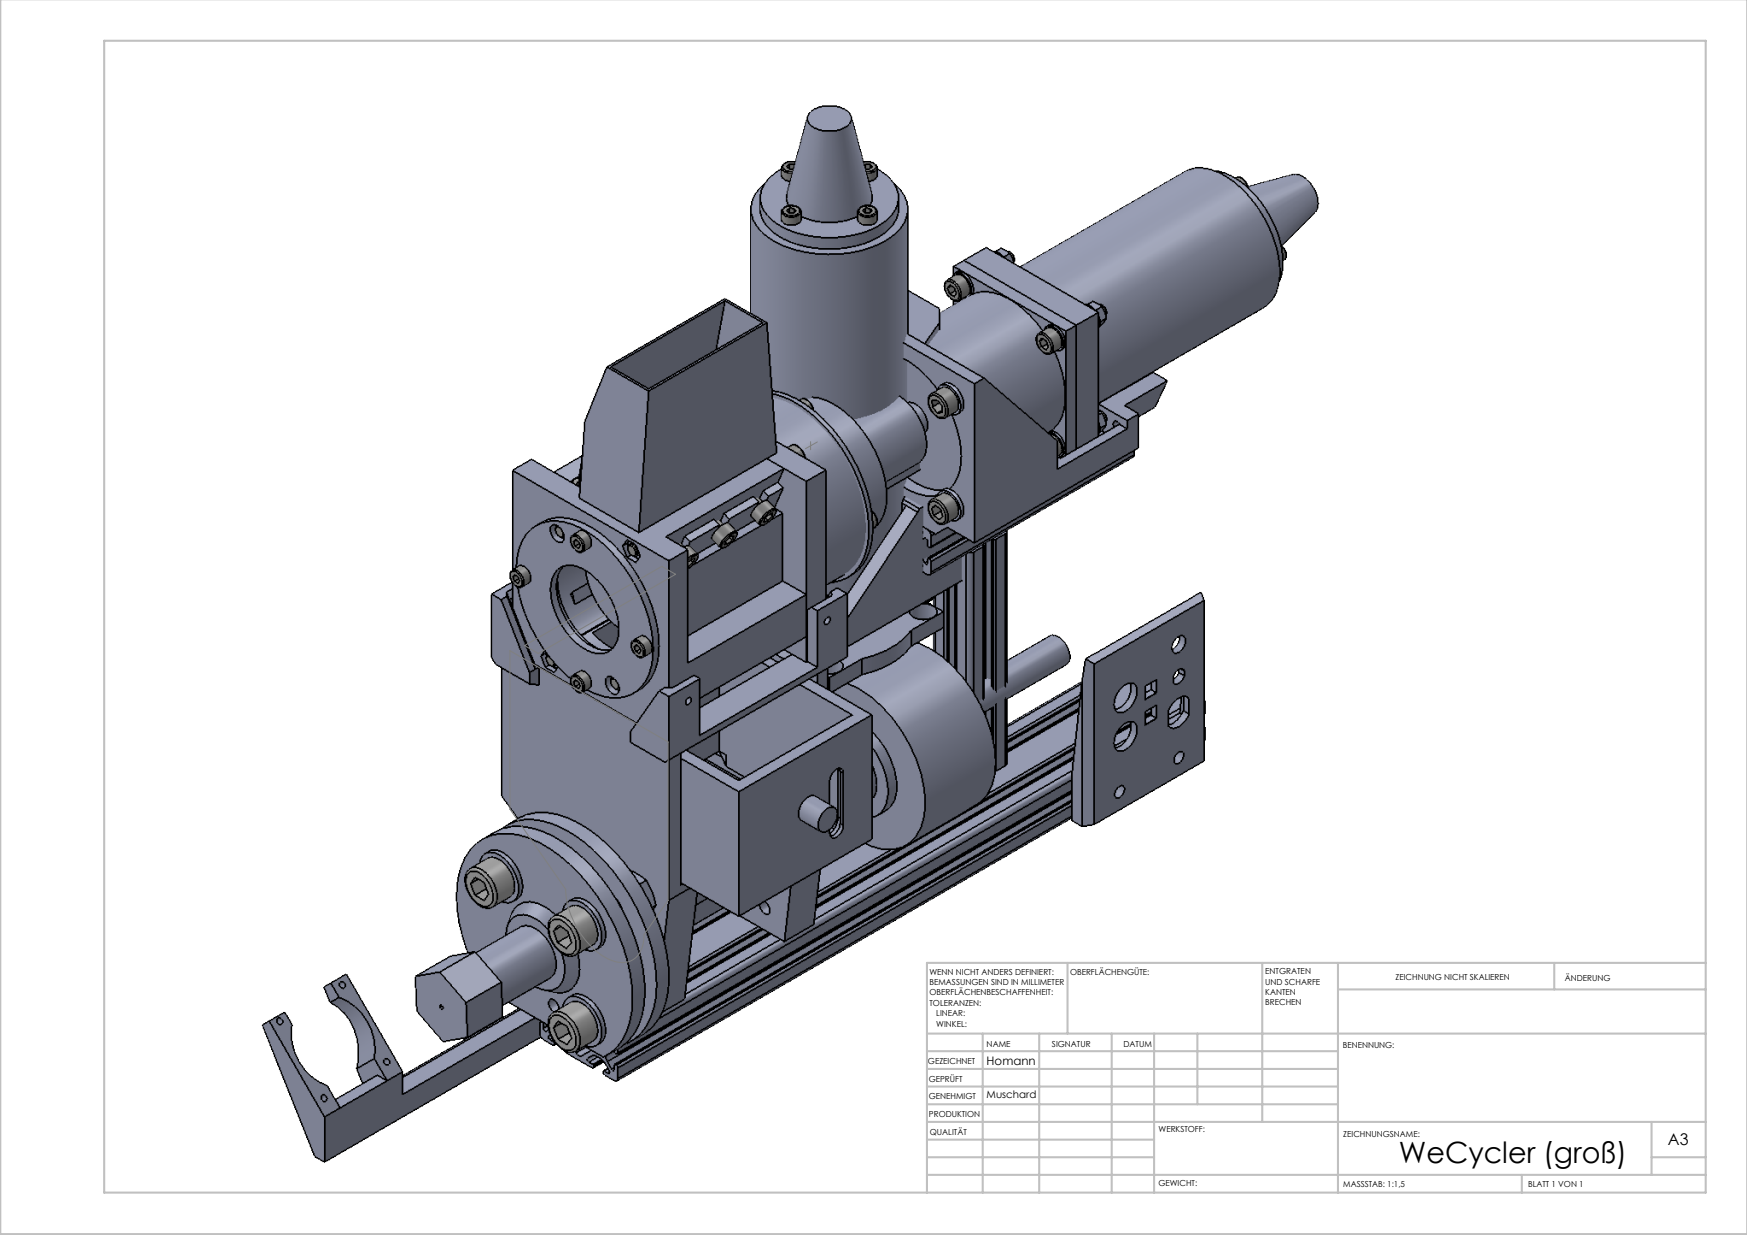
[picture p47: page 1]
MASSSTAB: 1:1,5; BLATT 1 VON 1; ZEICHNUNG NICHT SKALIEREN; ÄNDERUNG; UND SCHARFE; WENN NICHT ANDERS DEFINIERT:; OBERFLÄCHENGÜTE:

BEMASSUNGEN SIND IN MILLIMETER
OBERFLÄCHENBESCHAFFENHEIT:
TOLERANZEN:
LINEAR:
WINKEL:

NAME | SIGNATUR | DATUM | | | | BENENNUNG:

GEZEICHNET | Homann
GEPRÜFT
GENEHMIGT | Muschard
QUALITÄT | | | | WERKSTOFF: | ZEICHNUNGSNAME: WeCycler (groß) GEWICHT: | A3

PRODUKTION

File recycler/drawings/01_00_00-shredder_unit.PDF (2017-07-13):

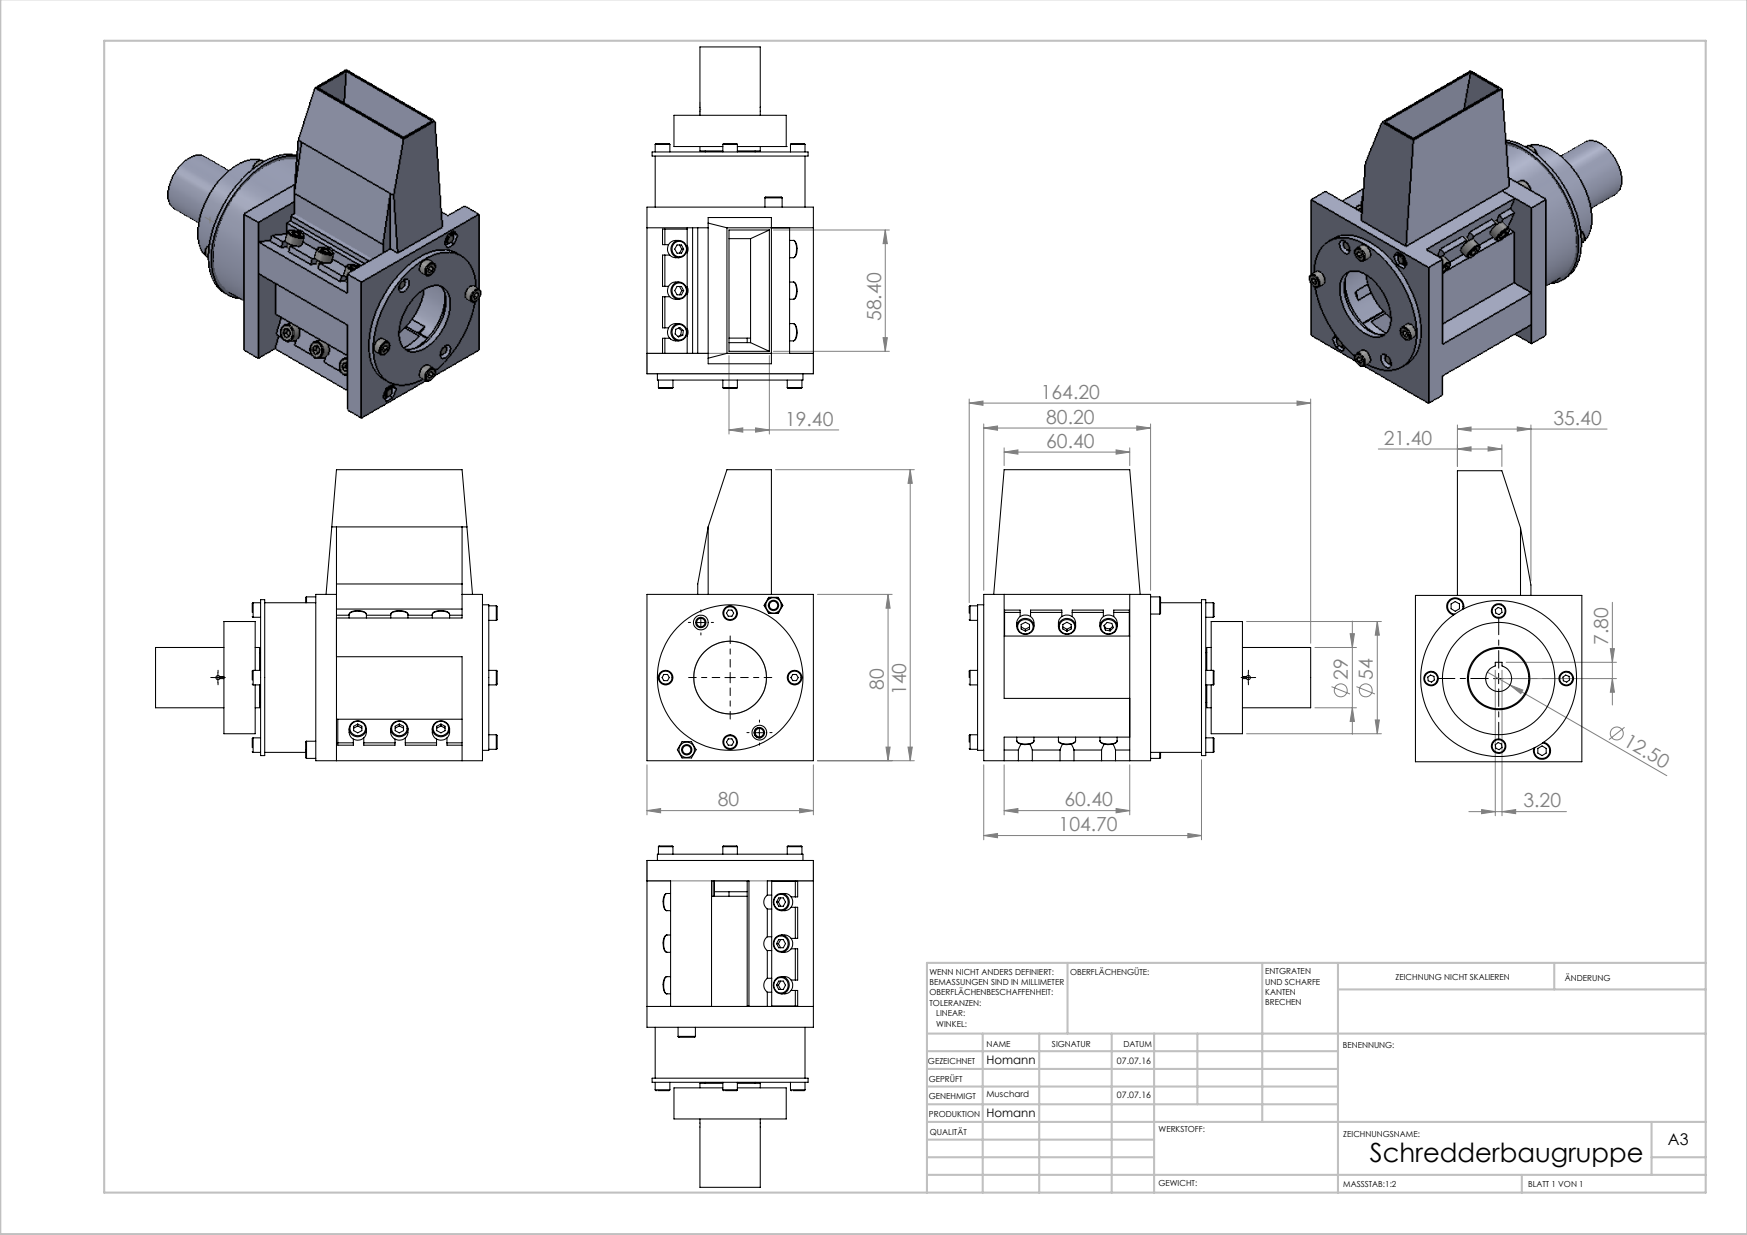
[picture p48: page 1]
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

BEMASSUNGEN SIND IN MILLIMETER
OBERFLÄCHENBESCHAFFENHEIT:
TOLERANZEN:
LINEAR:
WINKEL:

NAME | SIGNATUR | DATUM | | | | BENENNUNG:

GEZEICHNET | Homann | | 07.07.16

GEPRÜFT
GENEHMIGT | Muschard | | 07.07.16
PRODUKTION | Homann
QUALITÄT | | | | WERKSTOFF: | ZEICHNUNGSNAME: Schredderbaugruppe GEWICHT: | A3

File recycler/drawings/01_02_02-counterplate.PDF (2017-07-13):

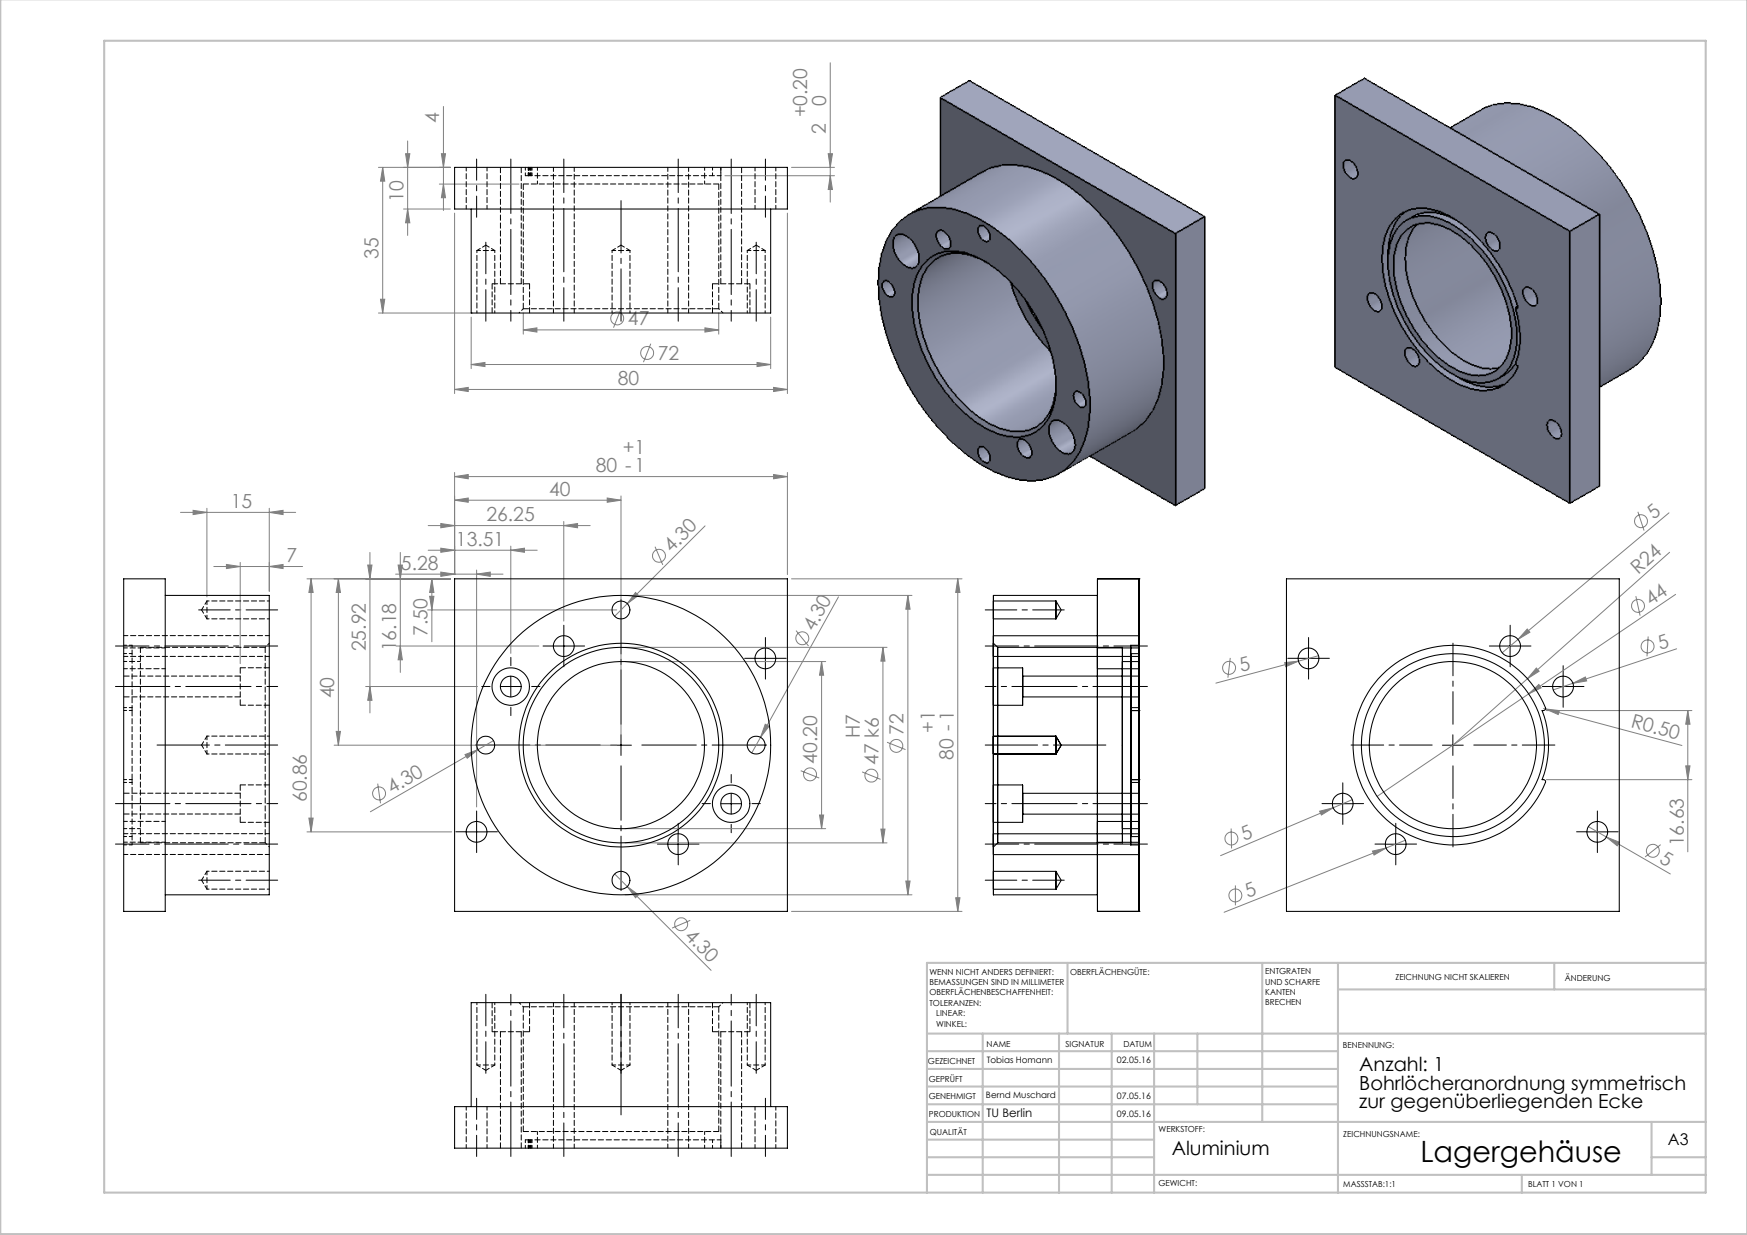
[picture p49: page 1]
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

BEMASSUNGEN SIND IN MILLIMETER
OBERFLÄCHENBESCHAFFENHEIT:
TOLERANZEN:
LINEAR:
WINKEL:

NAME | SIGNATUR | DATUM | | | | BENENNUNG: Anzahl: 1 Bohrlöcheranordnung symmetrisch zur gegenüberliegenden Ecke

GEZEICHNET | Tobias Homann | | 02.05.16
GEPRÜFT
GENEHMIGT | Bernd Muschard | | 07.05.16
PRODUKTION | TU Berlin | | 09.05.16
QUALITÄT | | | | WERKSTOFF: Aluminium | ZEICHNUNGSNAME: Lagergehäuse GEWICHT: | A3

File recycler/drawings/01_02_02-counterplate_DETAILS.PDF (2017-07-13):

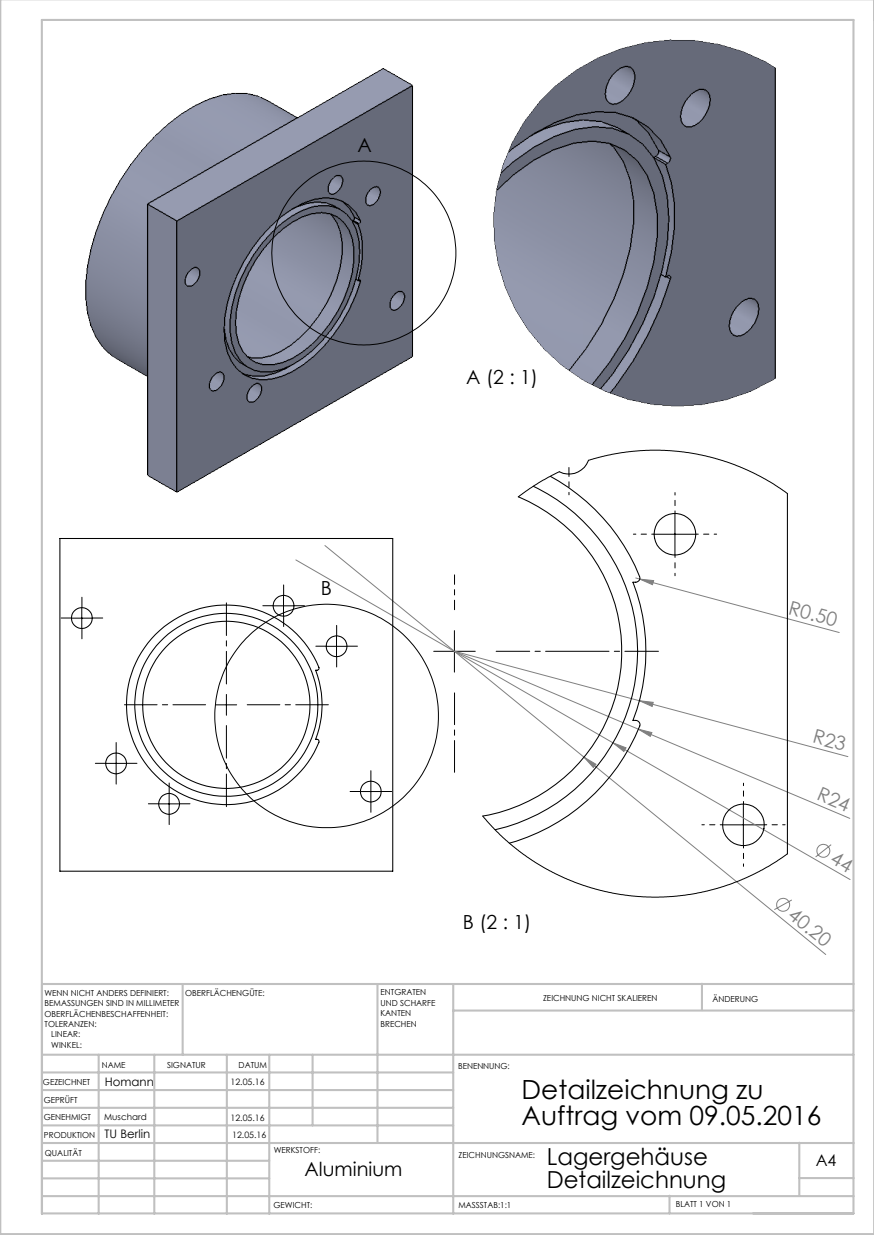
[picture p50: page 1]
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

BEMASSUNGEN SIND IN MILLIMETER
OBERFLÄCHENBESCHAFFENHEIT:
TOLERANZEN:
LINEAR:
WINKEL:

NAME | SIGNATUR | DATUM | | | | BENENNUNG: Detailzeichnung zu Auftrag vom 09.05.2016

GEZEICHNET | Homann | | 12.05.16
GEPRÜFT
GENEHMIGT | Muschard | | 12.05.16
PRODUKTION | TU Berlin | | 12.05.16
QUALITÄT | | | | WERKSTOFF: Aluminium | Lagergehäuse ZEICHNUNGSNAME: Detailzeichnung GEWICHT: | A4

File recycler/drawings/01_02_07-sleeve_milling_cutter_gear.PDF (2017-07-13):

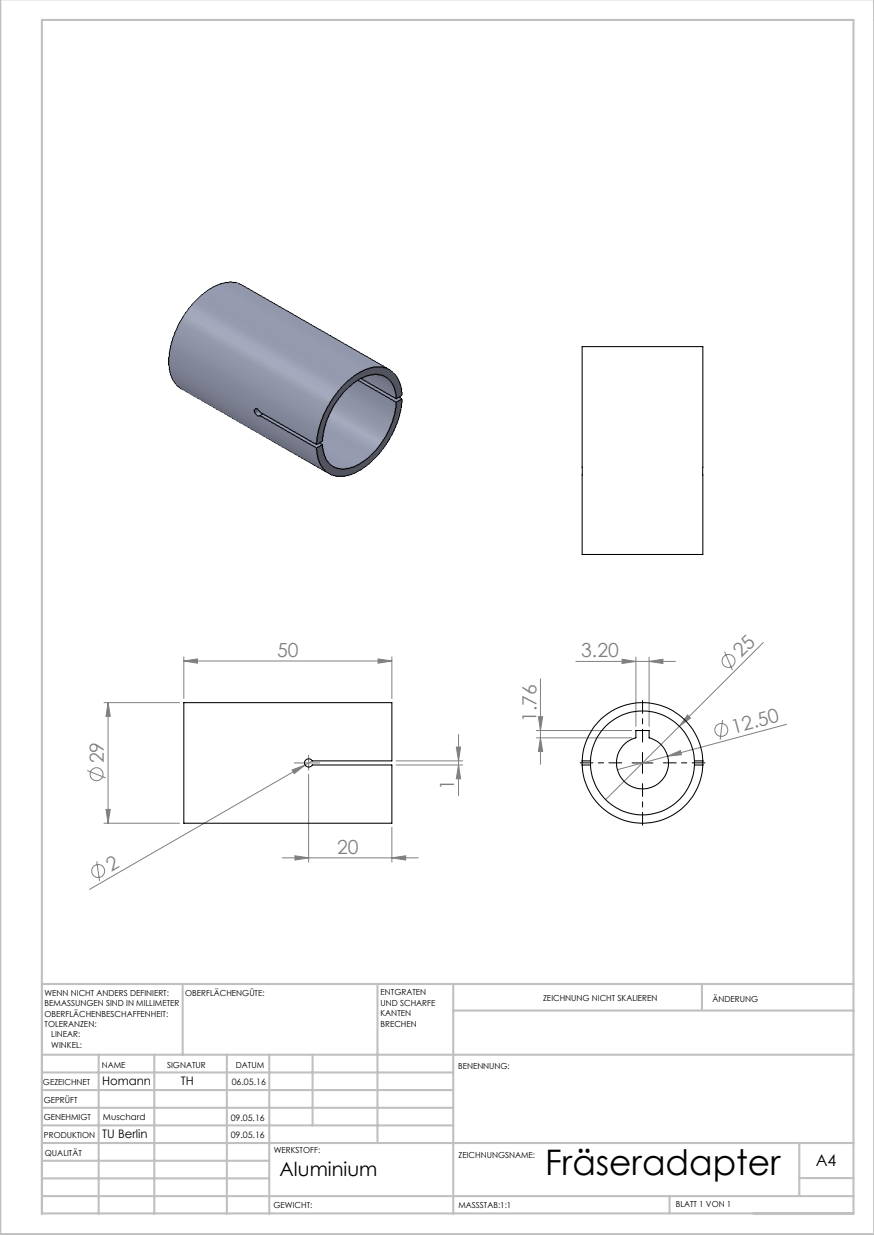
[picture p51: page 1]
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

BEMASSUNGEN SIND IN MILLIMETER
OBERFLÄCHENBESCHAFFENHEIT:
TOLERANZEN:
LINEAR:
WINKEL:

NAME | SIGNATUR | DATUM | | | | BENENNUNG:
QUALITÄT | | | | WERKSTOFF: Aluminium | Fräseradapter GEWICHT: ZEICHNUNGSNAME: | A4

GEZEICHNET | Homann | TH | 06.05.16

GEPRÜFT
GENEHMIGT | Muschard | | 09.05.16
PRODUKTION | TU Berlin | | 09.05.16

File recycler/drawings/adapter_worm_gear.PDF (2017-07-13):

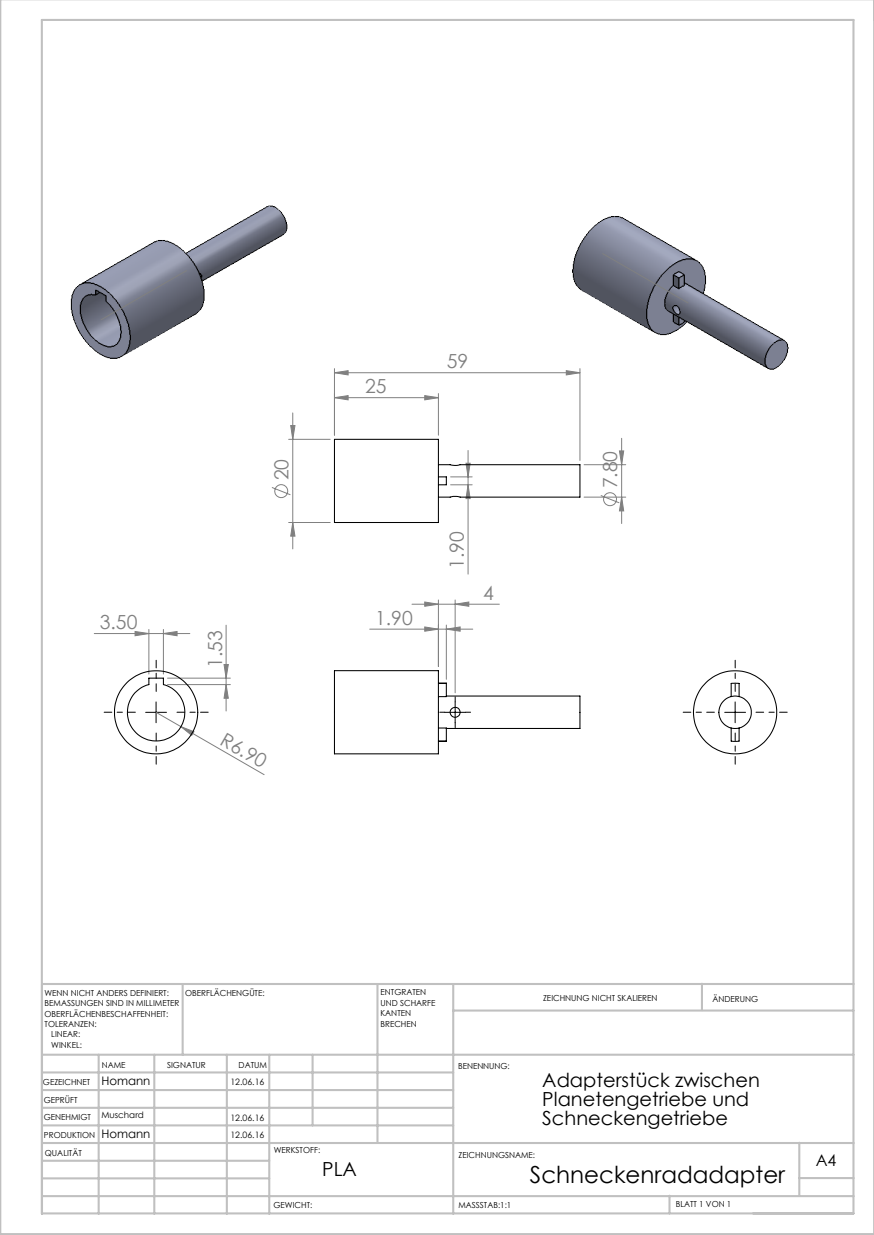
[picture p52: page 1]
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

BEMASSUNGEN SIND IN MILLIMETER
OBERFLÄCHENBESCHAFFENHEIT:
TOLERANZEN:
LINEAR:
WINKEL:

NAME | SIGNATUR | DATUM | | | | BENENNUNG: Adapterstück zwischen Planetengetriebe und Schneckengetriebe

GEZEICHNET | Homann | | 12.06.16

GEPRÜFT
GENEHMIGT | Muschard | | 12.06.16
PRODUKTION | Homann | | 12.06.16
QUALITÄT | | | | WERKSTOFF: PLA | ZEICHNUNGSNAME: Schneckenradadapter | A4

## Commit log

2017-06-03 Create power_supply
2017-06-30 order sortieren beispiel
    [DN15_Rohr_40.step, Duese.step, Extruder_DN15.step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]
2017-07-07 zwischenstand_etwas mehr struktur in ordner und text
2017-07-07 cad beispiel
2017-07-13 step, stl und explosions-files hinzugefügt
    [Abstandshalter_Fraeser.step, Adaperplatte_Motor_Planetengetriebe.step, Akku.step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]
2017-07-14 stl test
2017-07-14 extrudergruppe umgeordnet
    [DN15-1 Schneckengetriebe_vereinfacht.STL, DN15_Rohr_40.STL, Duese.STL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]
2017-07-14 extruder struktur feinschliff
    [Extruder_DN15_expl.STL, Extrudergruppe_expl.STL]
2017-07-16 WeCycler mit nur einer Antriebsgruppe hochladen
    [Wecycler - Extruder_Schublade-1.STL, Wecycler - Extrudergruppe-2 DN15_Rohr_100-1.STL, Wecycler - Extrudergruppe-2 Extruder_DN15-1 DN15_Rohr_40-1.STL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]
2017-07-27 neue cad struktur und nomenklatur hochladen
    [00_00_00-wecycler(explosion).SLDDRW, 00_00_00-wecycler.SLDASM, 01_00_00-shredderunit(explosion).SLDDRW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]
2017-07-27 begonnen mit readmeaktualisierung explosionsdarstellungen
    [02_00_00-extruder unit(explosion).STL, 02_00_00-extruder_unit(explosion).STL, 02_00_00-extruder_unit.STL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]
2017-07-27 explosionsdarst > exploded view; explosionreadmes.
    [02_00_00-extruder unit(explosion).STL, 02_00_00-extruderunit(explosion).STL]
2017-07-27 howto for cad files
2017-07-27 ordner umbenannt
    [00_00_00-wecycler(explosion).SLDDRW, 00_00_00-wecycler.SLDASM, 01_00_00-shredderunit(explosion).SLDDRW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]
2017-07-28 doppelte explosionsdarstellungen gelöscht
    [02_00_00-extruder unit(explosion).STL]
2017-07-28 alte cad daten entfernt
    [Abstandshalter_Fraeser.step, Adaperplatte_Motor_Planetengetriebe.step, Akku.step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]
2017-08-03 cad files alle mit _unit und powertrain anstatt drivetrain
    [00_00_00-wecycler.SLDASM, 01_00_00-shredder_unit(explosion).SLDDRW, 01_00_00-shredder_unit.SLDASM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]
2017-08-03 ordnername > englisch
    [Antriebsgruppe.SLDDRW, Extruderbaugruppe.SLDDRW, Extruderschnecke.SLDDRW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]
2017-08-20 Added Recycler BOM
    [BOM WeCycler.ods]
2017-08-20 Recycler BOM reupload
    [BOM_WeCycler.ods]
